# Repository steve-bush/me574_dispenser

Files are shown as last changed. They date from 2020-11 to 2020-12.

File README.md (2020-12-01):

# Plague Destroyer 3000

Below are the steps for setting up group 6's hand sanitizer dispenser for either home use or company use. The files for setting up the logoff scripts are located in the `logoff_scripts` directory. The part files for 3D printing are located in the `printing` directory. Lastly, the Arduino code is located in the `dispenser` directory.

## Printing

Use whatever printing software you prefer for slicing the STL files. We used Cura for our own set up to get usable G code. We used PLA+ at 225 C ejection temperature, 75 C bed temperature, 55% infill, a wall count of 3, and a 45 mm/s print speed.

## Assembly

1. Watch instruction [video](https://youtu.be/RnLYFoYw21w) for more information on the following steps.
2. Assemble PCB board according to the [schematic](https://github.com/steve-bush/me574_dispenser/blob/master/pcb/PCB_Schematic.PNG) and [BOM](https://github.com/steve-bush/me574_dispenser/blob/master/pcb/BOM_PCB%20Design_2020-11-05_15-47-10.csv) provided.
3. Drill 3/8in hole into top corner of sanitizer bottle.
4. Assemble Base Lid to Top using provided dowel pins.
5. Route USB cable through base inserting mini USB through bottom of base leaving 3 in of cable through top of base. Make sure USB cable is secured into notch on bottom of base.
6. Attach Pump to Pump Holder, making sure the suction port of the pump is at the base of the Pump Mount.
7. Install tubing into pump outlet, use twisting motion for proper installation.
8. Insert Pump and Pump mount into sanitizer bottle. Making sure that pump mount is sitting flush with the sanitizer bottle and pump outlet is facing towards hole in bottle.
9. Route wiring from pump and tubing through grommet hole in sanitizer bottle from the inside of the bottle to the outside.
10. Slide grommet over electrical cable beyond heat shrink tubing, then squeeze and insert tubing through grommet.
11. Insert grommet securely into hole of bottle.
12. Install grommet into sanitizer bottle.
13. Install sanitizer bottle into base with tubing towards right side of base when viewing from bottle side.
14. Insert LED holder into Top.
15. Mount assembled Base Lid and Top to the base using 2 of the provided screws, making sure USB cable and tubing is routed through slot in base and to not overtighten screws.
16. Flip assembly onto top.
17. Route tubing to far side of Top ensuring enough tube is allowed to reach nozzle.
18. Plug USB cord into Arduino Nano on PCB Board.
19. Insert PCB board into Top above tubing and secure with 2 of the provided screws making sure that the red/green Led is secured into LED holder and tubing and wiring is not pinched.
20. Install top cover making sure tubing is aligned with nozzle.
21. Plug in motor to motor wire from PCB board with correct polarity.
22. Install sanitizer bottle lid onto bottle.
23. Install mid cover onto front of sanitizer.
24. Plug in USB to 5V 1A power source or Computer USB port.

## Software

There are 2 different scripts than can be chosen from to enable the device to block login. The first script is `dispenser_ping_secure.ps1` which is the recommended script to use. It will block login whether the dispenser is plugged in or not. The other script named, `dispenser_ping.ps1`, will stop working when the device is unpluggled which may be desired for people without much computer knowledge.

When setting up the script to be run on login, the company's administrative software should be used and set up to run for non-admin or non-IT users. I give steps below to setting it up with Windows Group Policy and also with Task Scheduler. These would be available to anyone and the steps should be similar for whatever other administrative software used.

To setup using Group Policy:
1. Download files from GitHub.
2. Open mmc from the Windows search bar
3. Select File > Add/Remove Snap-in..
4. Select the Group Policy Object from the snap-in list
5. Click Add >
6. Select Browse.. then Users on the top options
7. Select Non-Administrators then OK
8. Click OK and double-click on the policy object
9. Select User Configuration > Windows Settings > Scripts (Logon/Logoff) > Logon
10. Select add and move the .ps1 file into the default browsing location (it will be hidden)
11. Now go back to the add screen and select the .ps1 file
12. Close and save the mmc screen

To setup with Task Scheduler:
1. Open Task Scheduler from the Windows search bar
2. Select Create Task...
3. Set the name to whatever you like, the group that is desired, and configuration to Windows 10.
4. Under the Triggers tab, select New and then set task to run on login
5. Under the Actions tab, select New and set the task to run either Powershell script
6. Close and save the new task.

Lastly, the Arduino [code](https://github.com/steve-bush/me574_dispenser/tree/master/dispenser) will need to be uploaded to either an Arduino Nano or Mega.

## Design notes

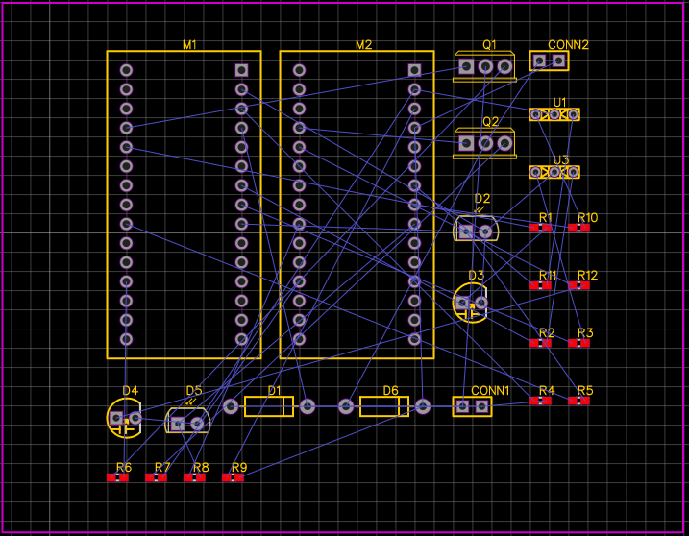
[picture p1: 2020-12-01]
pcb/PCB_Schematic.PNG

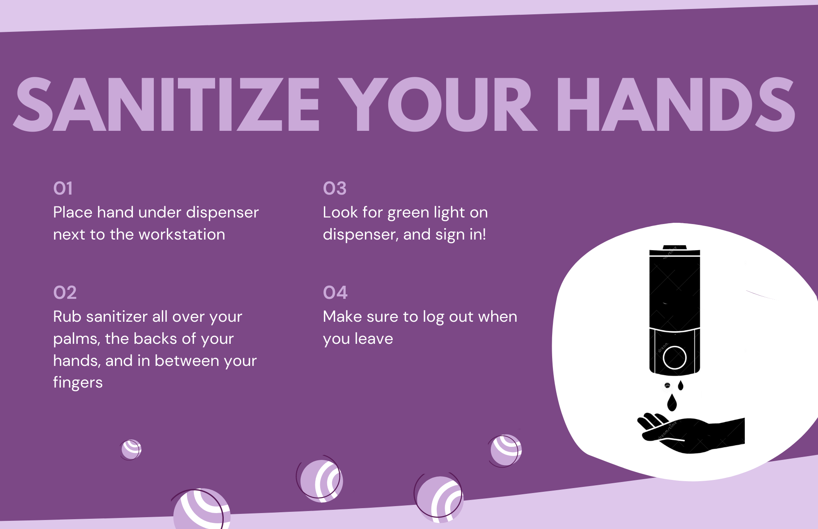
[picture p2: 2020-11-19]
Blue_and_White_Handwashing_101_Landscape_COVID_Flyer.png

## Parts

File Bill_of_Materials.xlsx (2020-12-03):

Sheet: Bill of Materials
Bill of Materials
Item # | Item | Part Number | Source | Cost | Qty. | Ext. Cost | Item # | Link
1 | 3x5mm Silicon Rubber Tubing | 372114317823 | Ebay, giorgio11185 | $14.36 | 0.01333333333 | $0.19 | 1 | https://www.ebay.com/itm/US-Stock-50ft-OD-5mm-ID-3mm-Silicone-Food-Grade-Rubber-Tube-Hose-Pipe/372114317823
2 | Jar w/Cap | 137579 | US Plastic Corp | $0.87 | 1 | $0.87 | 2 | https://www.usplastic.com/catalog/item.aspx?itemid=137579
3 | Submersible Pump | 292F517 | Alibaba, Fbele | $0.33 | 1 | $0.33 | 3 | https://www.alibaba.com/product-detail/DC-3V-mini-water-pump-Horizontal_1600055883828.html
4 | PCB |  | PCBWay | $0.62 | 1 | $0.62 | 4
5 | 3ft USB type A to type B mini | 3021055-03 | Mouser | $0.98 | 1 | $0.98 | 5 | https://www.mouser.com/ProductDetail/Qualtek/3021055-03?qs=MLItCLRbWswd6xwF2kMv5g%3D%3D
6 | Rubber Grommet 1/4" ID, 3/8" slot diamter | 9600K25 | McMastercarr | $0.07 | 1 | $0.07 | 6 | https://www.mcmaster.com/9600K25/
7 | #4 x 3/4" Thread Forming Screws for Plastics (48-2) / Phillips / Pan Head / Steel / Zinc | 231428 | Fastener Super Store | $0.01 | 4 | $0.06 | 7 | https://www.fastenersuperstore.com/products/231428/thread-forming-screws
8 | Base - injection molded |  | Xometry | $1.20 | 1 | $1.20 | 8
9 | Base Lid - IM |  | Xometry | $1.02 | 1 | $1.02 | 9
10 | Mid Level Cover - IM |  | Xometry | $0.75 | 1 | $0.75 | 10
11 | Top - IM |  | Xometry | $1.42 | 1 | $1.42 | 11
12 | Top Cover - IM |  | Xometry | $1.04 | 1 | $1.04 | 12
13 | Pump holder - IM |  | Xometry | $0.40 | 1 | $0.40 | 13
14 | Tooling cost per unit |  | Xometry | $1.12 | 1 | $1.12 | 14
15 | Labor Cost (USA) |  | USA Labor (PayScale) | $13.45 | 0.088736 | $1.19 | 15 | https://www.payscale.com/research/US/Job=Assembly_Line_Worker/Hourly_Rate
 |  |  |  |  | Total | $11.26
 | Tooling cost |  |  | $31221.00

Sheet: 2nd and 3rd Quotes
2nd and 3rd Quotes
Item # | Item | Part Number | Source | Cost | Qty. | Ext. Cost | Item # | Link
1 | 3mm x 5mm Silicon tubing | 3184K288 | McMaster-Carr | $0.67 | 1 | $0.67 | 1
1 | 3mm x 5mm Silicon tubing | SKU: ST-35 | MODDIY | $0.99 | 0.6666666667 | $0.66 | 1 | https://www.moddiy.com/products/High-Quality-Food-Grade-Flexible-Silicone-Tubing-3mm-ID-x-5mm-OD.html
1 | 3x5mm Silicon Rubber Tubing |  | Ebay, giorgio11185 | $14.36 | 0.01333333333 | $0.19 | 1 | https://www.ebay.com/itm/US-Stock-50ft-OD-5mm-ID-3mm-Silicone-Food-Grade-Rubber-Tube-Hose-Pipe/372114317823
2 | 32oz Clear PET container with grips without cap | 3471B03-B | Berlin Packaging | $0.96 | 1 | $0.96 | 2 | https://www.berlinpackaging.com/3471b03-b-32-oz-clear-petg-plastic-gripper-containers-cap-not-included/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
2 | Clear PET 32oz Jar/cap | CP-B124 | Premium Vials | $159.99 | 0.007936507937 | $1.27 | 2 | https://www.premiumvials.com/pk-of-126-32-oz-clear-pet-square-grip-container-with-89-400-neck-finish/
2 | Jar w/Cap |  | US Plastic Corp | $0.87 | 1 | $0.87 | 2 | https://www.usplastic.com/catalog/item.aspx?itemid=137579
3 | Submersible pump, 3-5v | B08D986N3V | Amazon - Sen Mod | $12.99 | 10 | $1.30 | 3 | https://www.amazon.com/Senmod-Silent-Submersible-Computer-Cooled/dp/B08D986N3V?hvadid=475811883826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
3 | Submersible pump 3-6v | #00002 | Ebay - Light in the Box | $4.19 | 1 | $4.19 | 3 | https://www.google.com/shopping/product/1?q=5v+aquarium+pump
3 | Submersible Pump, 5v |  | Alibaba, Fbele | $0.33 | 1 | $0.33 | 3 | https://www.alibaba.com/product-detail/DC-3V-mini-water-pump-Horizontal_1600055883828.html
4 | PCB |  | Rush PCB | $10.85 | 1 | $10.85 | 4
4 | PCB |  | PCBWay | $0.62 | 1 | $0.62 | 4
4 | PCB |  | 4PCB | $3.32 | 1 | $3.32 | 4
5 | 1ft USB2.0 A Male to Mini-B 5-pin Male Cable | U2105-1101 | Cable Leader | $0.77 | 1 | $0.77 | 5 | https://www.cableleader.com/1ft-usb2-0-a-male-to-mini-b-5-pin-male-cable.html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
5 | USB 2.0 Cable, A-Male/Mini B-Male, 5-Pin, Hi-Speed 480Mbps, 3FT | USB2-3017-ABM5 | Primus Cable | $1.13 | 1 | $1.13 | 5 | https://www.primuscable.com/products/usb-2-0-cable-a-malemini-b-male-5-pin-hi-speed-480mbps-1ft-3ft-6ft-10ft-15ft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
5 | 3ft USB type A to type B mini | 3021055-03 | Mouser | $0.98 | 1 | $0.98 | 5 | https://www.mouser.com/ProductDetail/Qualtek/3021055-03?qs=MLItCLRbWswd6xwF2kMv5g%3D%3D
6 | Rounded Head Thread-Forming Screws | 97349A418 | McMaster-Carr | $0.06 | 4 | $0.25 | 6 | https://www.mcmaster.com/97349A417/
6 | #4-20 x 3/4 in Zinc-Plated Case Hardened Steel Thread Forming Screw with Pan Head Type, 100 PK | 5JE99 | Grianger Industrial | $0.16 | 4 | $0.65 | 6 | https://www.grainger.com/product/TAMPER-PRUF-SCREW-4-20-x-3-4-in-Zinc-Plated-5JE99
6 | #4 x 3/4" Thread Forming Screws for Plastics (48-2) / Phillips / Pan Head / Steel / Zinc | 231428 | Fastener Super Store | $0.01 | 4 | $0.06 | 6 | https://www.fastenersuperstore.com/products/231428/thread-forming-screws
8 | Base - injection molded |  | Xometry | $1.20 | 1 | $1.20 | 8
8 | Base - injection molded |  | Texas Injection | $1.93 | 1 |  | 8
8 | Base - injection molded |  | Protolabs | $6.38 | 1 | $6.38 | 8
9 | Base Lid - IM |  | Xometry | $1.02 | 1 | $1.02 | 9
9 | Base Lid - IM |  | Texas Injection | $0.82 | 1 | $0.82 | 9
9 | Base Lid - IM |  | Protolabs | $3.81 | 1 | $3.81 | 9
10 | Mid Level Cover - IM |  | Xometry | $0.75 | 1 | $0.75 | 10
10 | Mid Level Cover - IM |  | Texas Injection | $1.04 | 1 | $1.04 | 10
10 | Mid Level Cover - IM |  | Protolabs | $4.70 | 1 | $4.70 | 10
11 | Top - IM |  | Xometry | $1.42 | 1 | $1.42 | 11
11 | Top - IM |  | Texas Injection | $0.99 | 1 | $0.99 | 11
11 | Top - IM |  | Protolabs | $4.61 | 1 | $4.61 | 11
12 | Top Cover - IM |  | Xometry | $1.04 | 1 | $1.04 | 12
13 | Pump holder |  | 3D Printed | $0.42 | 1 | $0.42 | 13
14 | Tooling cost per unit |  | Xometry | $1.00 | 1 | $1.00 | 14
14 | Tooling cost per unit |  | Texas Injection | $1.55 | 1 | $1.55 | 14
14 | Tooling cost per unit |  | Protolabs | $0.99 | 1 | $0.99 | 14
15 | Labor Cost (USA) |  | USA Labor (PayScale) | $13.45 | 0.088736 | $1.19 | 15 | https://www.payscale.com/research/US/Job=Assembly_Line_Worker/Hourly_Rate

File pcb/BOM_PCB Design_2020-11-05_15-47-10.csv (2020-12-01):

ID | Name | Designator | Footprint | Quantity | Manufacturer Part | Manufacturer | Supplier | Supplier Part
1 | IRF510 | Q1,Q2 | TO220 | 2 | IRF510PBF | IR | LCSC | C2596
2 | MICROCONTROLLER | M1,M2 | ARDUINO NANO | 2 | PIC18F2321-I/SO | Microchip Tech | LCSC | C184141
3 | IR LED | D3,D4 | LED2-2.54-D5.0MM | 2 | 2A5Y3UD09 LED | KENTO | LCSC | C3651
4 | 2 pin header | CONN1,CONN2 | 2 PIN HEADER | 2 | Female header1*2P | BOOMELE | LCSC | C66509
5 | 120 OHM | R4,R9 | 0603-RES | 2 | 1206W4J0124T5E | UniOhm | LCSC | C25648
6 | PHOTODIODE | D2,D5 | PHOTODIODE_SFH225 | 2 | DK5V45R10 | DK | LCSC | C94730
7 | DIODE IN4001 | D1,D6 | DIODE-1N4001 | 2 | DK5V45R10 | DK | LCSC | C94730
8 | RG LED | U3,U1 | LED-DUALCOLOR-3MM | 2 | 3528 Red LED | KENTO | LCSC | C2305
9 | 300OHM-1_10W-1%(0603) | R1,R12 | 0603-RES | 2 | RD 3WS 300R J T/B A1 | TyoHM | LCSC | C433811
10 | 300 OHM | R2,R3,R10,R11 | 0603-RES | 4 | SMF 3W 300R J | TyoHM | LCSC | C395116
11 | 10k OHM | R5,R6,R7,R8 | 0603-RES | 4 | MF58 103F3435 | Nanjing Shiheng Elec | LCSC | C123387

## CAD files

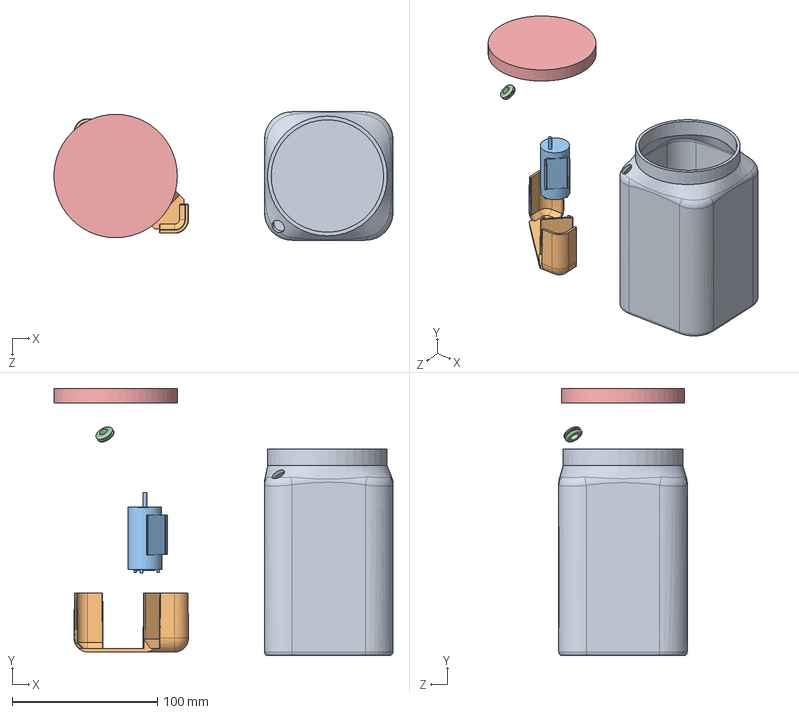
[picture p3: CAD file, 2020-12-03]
solidworks/Bottle Assembly.SLDASM
233.7 x 184.3 x 88.6 mm
Bottle
Pump holder
Liquid Pump
Rubber Grommet
BottleLid

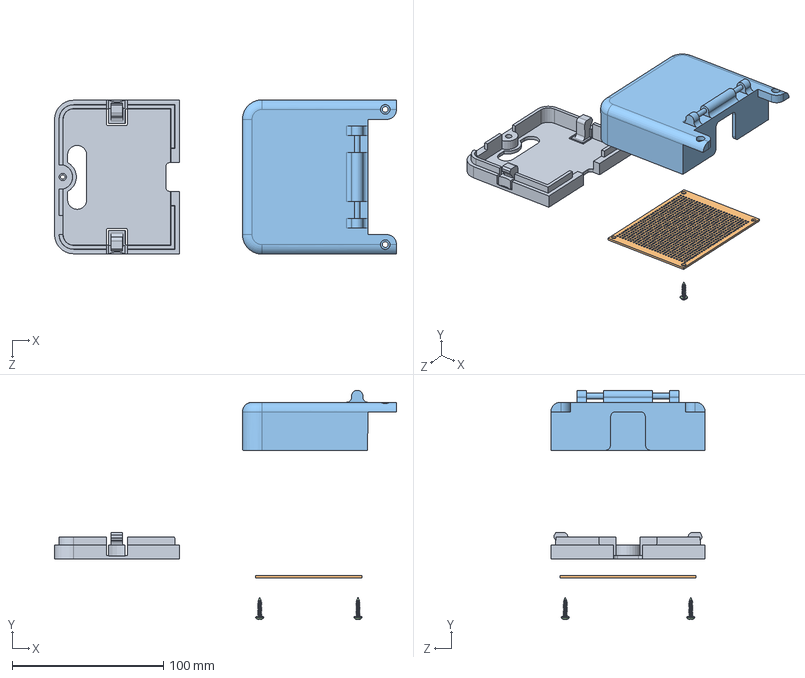
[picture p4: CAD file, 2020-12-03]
solidworks/Top Assembly.SLDASM
226.1 x 151.6 x 102.0 mm
Top Under Cover
Circuit Board
Top
92470A110_PAN HEAD PHILLIPS SCREW FOR SHEET METAL x 2

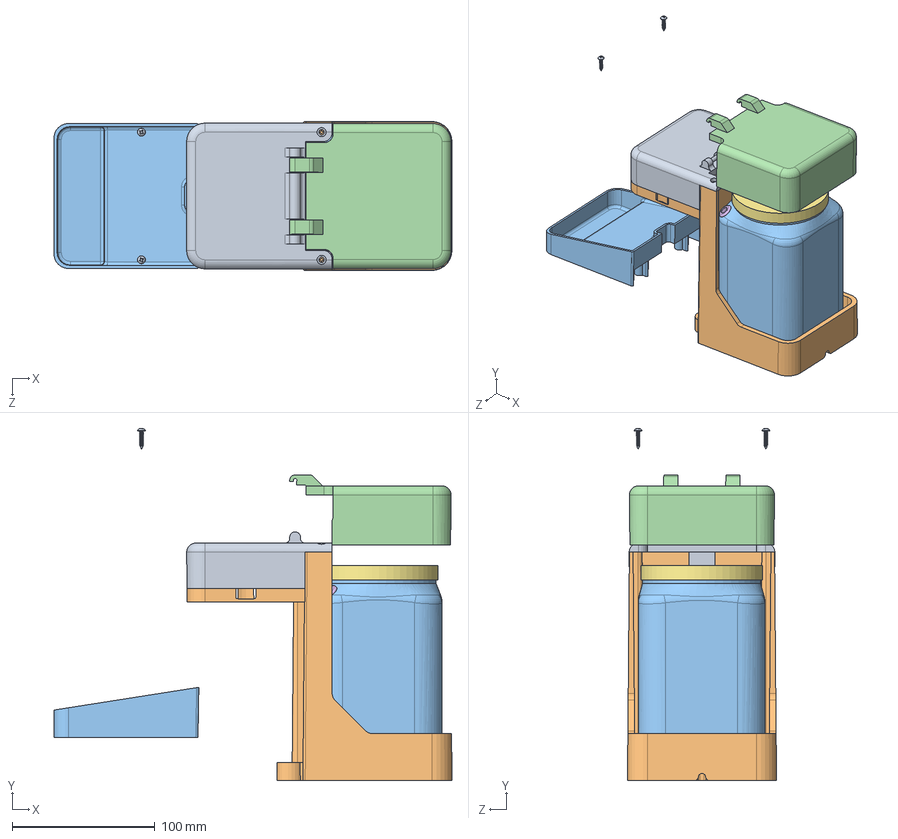
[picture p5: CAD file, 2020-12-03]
solidworks/Full Assembly.SLDASM
278.6 x 246.7 x 104.4 mm
Bottle
Pump holder
Liquid Pump
Rubber Grommet
BottleLid
Top Under Cover
Circuit Board
Top
92470A110_PAN HEAD PHILLIPS SCREW FOR SHEET METAL x 4
Base
Drip Tray
BaseLid

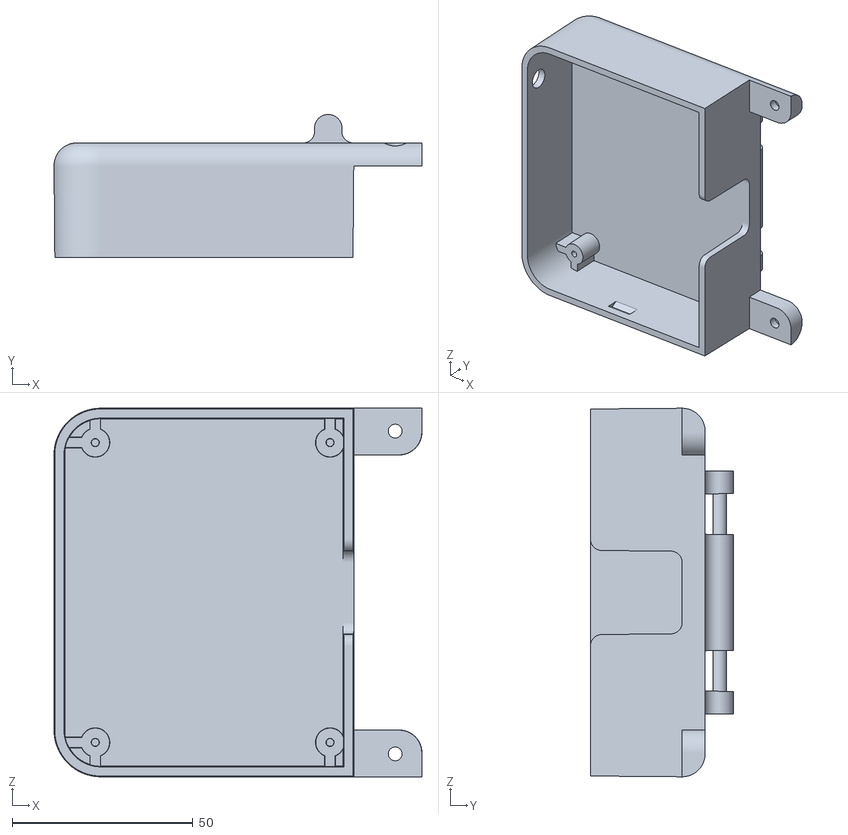
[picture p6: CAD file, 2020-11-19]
printing/Top 11_5.STL
101.9 x 39.6 x 102.0

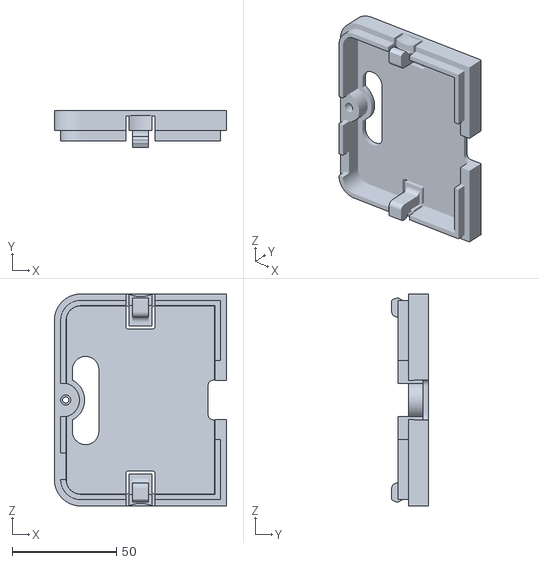
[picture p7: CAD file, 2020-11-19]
printing/Top cover10_15.STL
82.6 x 17.6 x 101.6

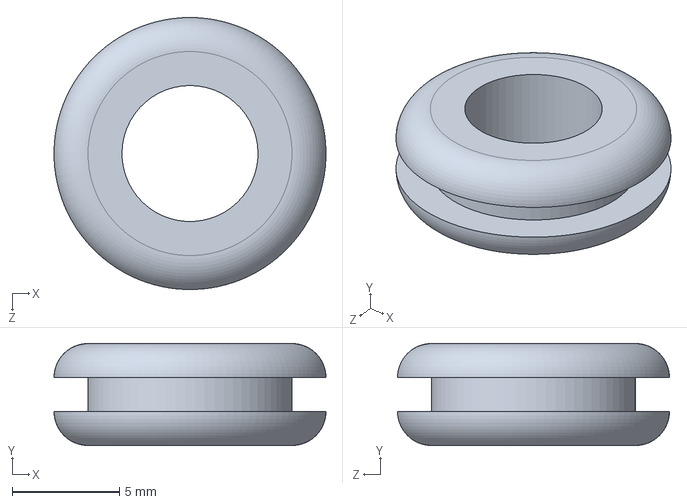
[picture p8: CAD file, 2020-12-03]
solidworks/Rubber Grommet.SLDPRT
12.7 x 4.76 x 12.7 mm

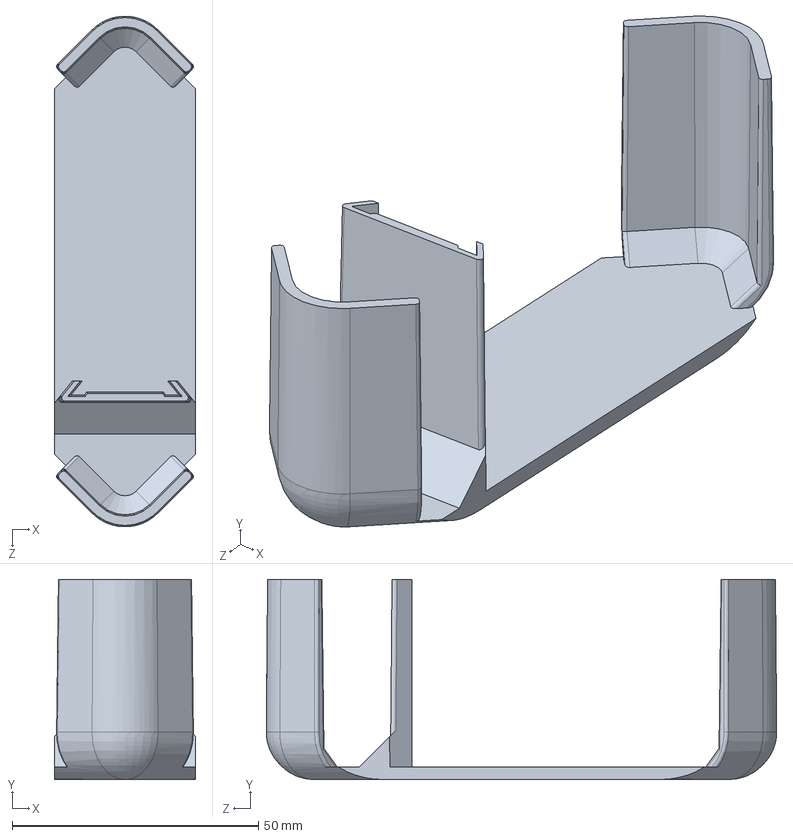
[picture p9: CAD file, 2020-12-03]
solidworks/Pump holder.SLDPRT
28.7 x 40.6 x 103.7 mm

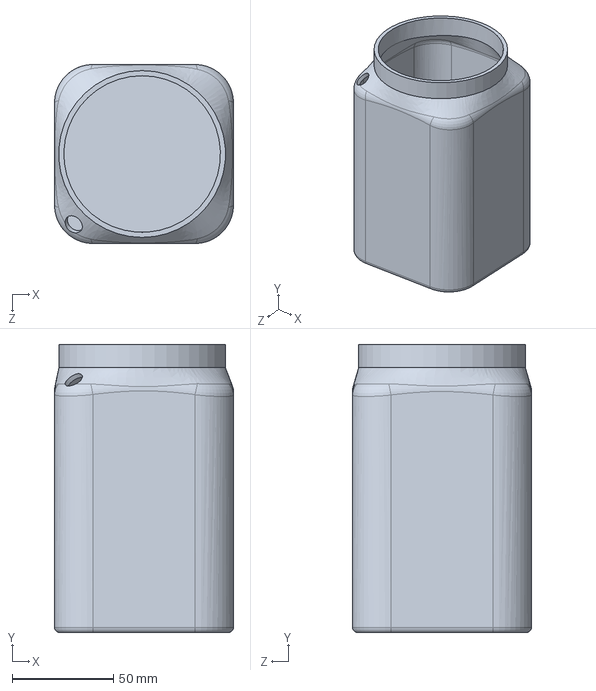
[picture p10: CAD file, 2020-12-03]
solidworks/Bottle.SLDPRT
88.6 x 142.5 x 88.6 mm

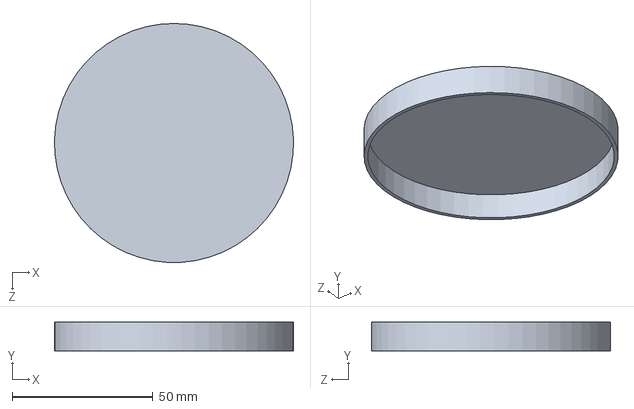
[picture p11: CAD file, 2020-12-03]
solidworks/BottleLid.SLDPRT
85.1 x 10.2 x 85.1 mm

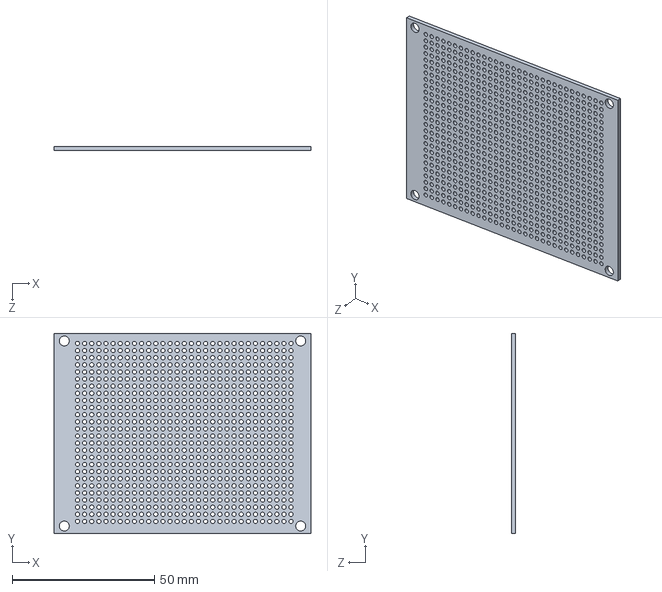
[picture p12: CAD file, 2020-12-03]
solidworks/Circuit Board.SLDPRT
90.2 x 70.2 x 1.50 mm

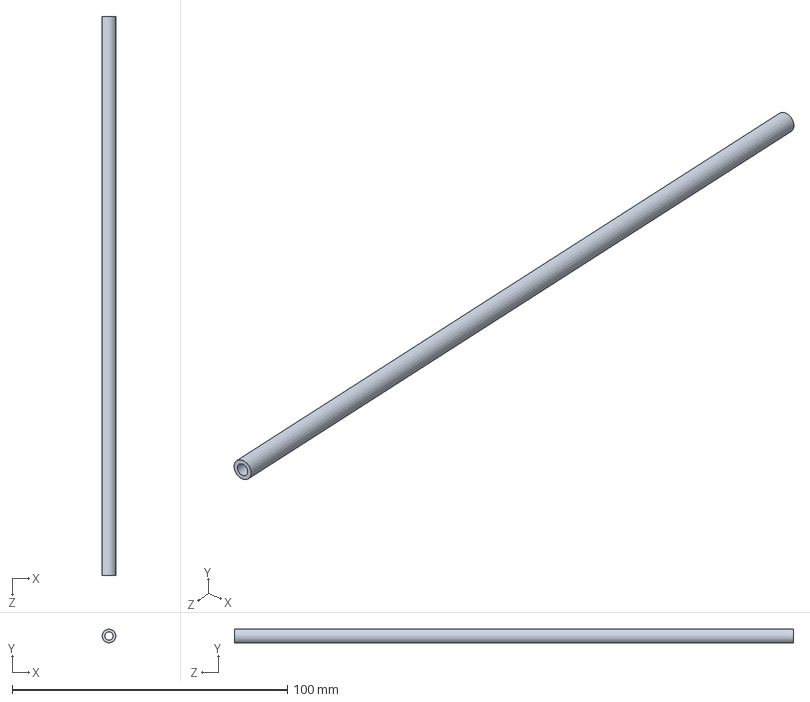
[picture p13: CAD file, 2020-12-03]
solidworks/Transfer Tube.SLDPRT
5.00 x 5.00 x 203.2 mm

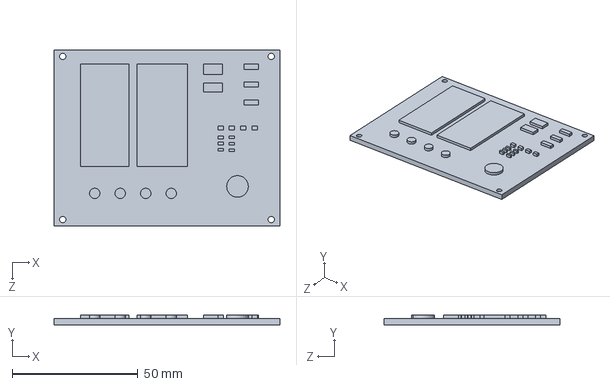
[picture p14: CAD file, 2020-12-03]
solidworks/PCB.SLDPRT
90.0 x 3.81 x 70.0 mm

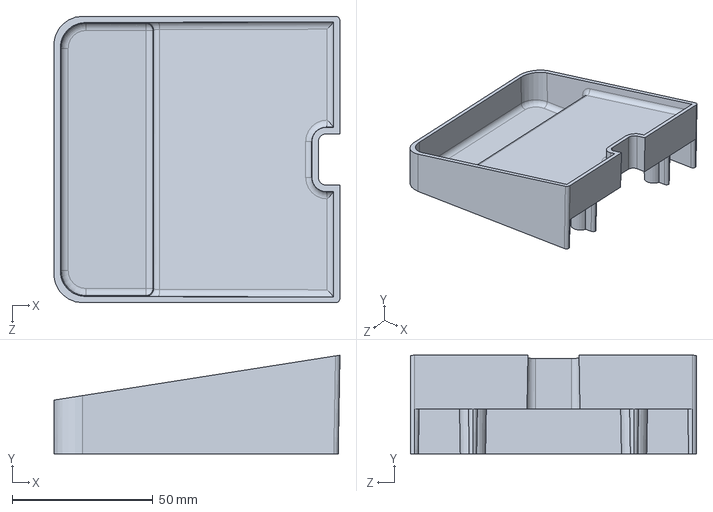
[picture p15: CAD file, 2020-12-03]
solidworks/Drip Tray.SLDPRT
101.4 x 35.0 x 101.6 mm

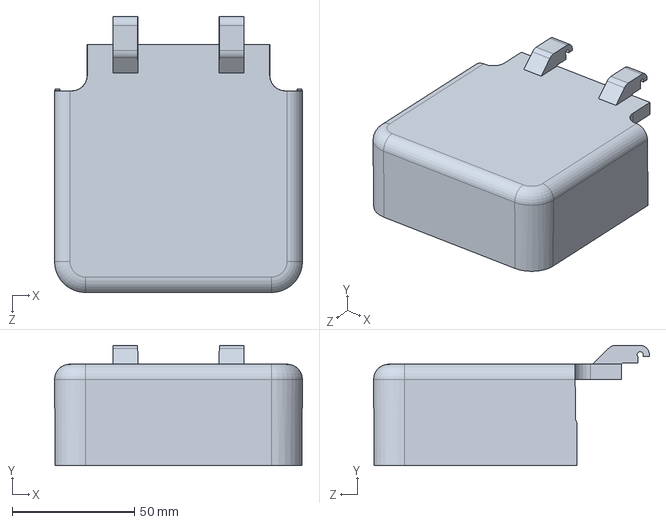
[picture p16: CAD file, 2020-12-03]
solidworks/BaseLid.SLDPRT
101.5 x 49.1 x 113.0 mm

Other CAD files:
solidworks/Top.SLDPRT
solidworks/Top Under Cover.SLDPRT
solidworks/Base.SLDPRT
solidworks/Liquid Pump.SLDPRT
printing/Base.STL
solidworks/92470A110_PAN HEAD PHILLIPS SCREW FOR SHEET METAL.SLDPRT

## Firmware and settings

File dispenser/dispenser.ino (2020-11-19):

#include "dispenser.h"

enum DispenserState { Unwashed, Dispense, Washed } dispenserState;
unsigned long SensorTime; // Timer for when sensor detects hand.
unsigned long WashTime; // Timer for end of washed state
unsigned long DispenseTime; // Timer for length of dispense state
bool wash_flag; // Flag for deciding what to send
unsigned int previous_readings[NUM_READINGS];
unsigned int new_readings[NUM_READINGS];
int index = 0;
// 1 minute 30 seconds to log on (milliseconds)
const unsigned long WASH_TIMEOUT = 90000;

void set_to_washed() {
  wash_flag = WASHED; // Indicate that button is pressed
  analogWrite(RED_LED, 0); // Turn off red first so both LEDs are not on
  analogWrite(GREEN_LED, 255); // Turn on green to indicate login time
  WashTime = millis(); // Begine wash_timer for timeout
}

void set_to_unwashed() {
  wash_flag = UNWASHED; // Indicate unwashed
  analogWrite(GREEN_LED, 0); // Turn off green first so both LEDs are not on
  analogWrite(RED_LED, 255); // Turn on red to indicate washing hands
}

void initialize_sensor() {
  // Set up the sensor reading arrayss
  for (int i = 0; i < NUM_READINGS; i++) {
    previous_readings[i] = analogRead(PHOTODIODE_SENSOR);
    new_readings[i] = analogRead(PHOTODIODE_SENSOR);
  }
}

bool read_sensor() {
  if (millis() - SensorTime < SENSOR_DELAY){
    return false;
  }
  //Add sensor reading into the array
  previous_readings[index] = new_readings[index];
  new_readings[index] = analogRead(PHOTODIODE_SENSOR);

  // Move index down the array
  index++;

  // Loop index back to 0 if past array bounds
  if (index > NUM_READINGS - 1) {
    index = 0;
  }

  // Initialize average readings variables
  float previous_ave = 0;
  float new_ave = 0;
  // Add up the previous and new readings arrays
  for (int i = 0; i < NUM_READINGS; i++) {
    previous_ave += previous_readings[i];
    new_ave += new_readings[i];
  }

  // Calculate the average of the readings
  previous_ave /= NUM_READINGS;
  new_ave /= NUM_READINGS;

  // Update SensorTime for delay
  SensorTime = millis();
  
  if (previous_ave - new_ave > THRESHOLD_CHANGE) {
    return true;
  }
  else {
    return false;
  }
}

void setup() {
  // Setup pins
  pinMode(GREEN_LED, OUTPUT);
  pinMode(RED_LED, OUTPUT);
  pinMode(MOTOR, OUTPUT);
  Serial.begin(9600); // Set baud rate to 9600.
  pinMode(PHOTODIODE_SENSOR, INPUT);
  pinMode(PHOTODIODE_POWER, OUTPUT);
  digitalWrite(PHOTODIODE_POWER, HIGH);
  pinMode(IR_LED, OUTPUT);
  digitalWrite(IR_LED, HIGH);
  set_to_unwashed();
  initialize_sensor();
  dispenserState = Unwashed; // Set state back to unwashed
} // setup()

void loop() {
  // Check for ping from pc
  if (Serial.available() > 0) {
    Serial.readString(); // Read in passed
    // Send state of wash_flag to pc
    if (wash_flag) {
      Serial.println("Washed"); // Indicate that hands have been washed
      set_to_unwashed();
      dispenserState = Unwashed; // Set state back to unwashed
    }
    else {
      Serial.println("Unwashed"); // Indicate that hands are not washed
    }
  }

  switch (dispenserState) {
    case Unwashed:
      if (read_sensor()) { // If hand detected.
        DispenseTime = millis(); // Record time of hand detection.
        analogWrite(MOTOR, 255);
        set_to_washed();
        dispenserState = Dispense; // Set state back to unwashed
      }
      break;

    case Dispense:
      read_sensor();
      if (millis() - DispenseTime >= DISPENCE_TIME) {
        analogWrite(MOTOR, 0);
        set_to_washed();
        dispenserState = Washed; // Set state to washed
      }
      break;

    case Washed:
      if (read_sensor() && millis() - DispenseTime >= DISPENCE_DELAY) { // If hand detected.
        analogWrite(MOTOR, 255);
        DispenseTime = millis(); // Record time of hand detection.
        dispenserState = Dispense; // Move to intial detection state.
      }
      else if (millis() - WashTime >= WASH_TIMEOUT) {
        set_to_unwashed();
        dispenserState = Unwashed; // Set state back to unwashed
      }
      break;
  }
} // loop()

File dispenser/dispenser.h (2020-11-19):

// Bools to be used for the wash_flag
#define WASHED true
#define UNWASHED false
// Pin assignments
#define RED_LED A5
#define GREEN_LED A4
#define MOTOR  9 // D9
#define PHOTODIODE_SENSOR A3
#define PHOTODIODE_POWER 2 //D2
#define IR_LED 6 // D6
// Threshold for defining hand detection.
#define THRESHOLD_CHANGE 30
#define NUM_READINGS 2
#define SENSOR_DELAY 100
// Amount of time to dispense.
#define DISPENCE_TIME 875 // .875 second
#define DISPENCE_DELAY 3000 // 3 seconds

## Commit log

2020-09-14 Added full prototype code, renamed powershell script, and rearanged folders
2020-11-19 Added more steps
    [Base.STL, Top 11_5.STL, Top cover10_15.STL]
2020-11-26 Formatting. Needs circuit
2020-11-26 Editting. Still needs circuitry
2020-12-01 Added circuit info
    [BOM_PCB Design_2020-11-05_15-47-10.csv]
2020-12-01 Circuit links
2020-12-03 BOM and Solidworks files
    [92470A110_PAN HEAD PHILLIPS SCREW FOR SHEET METAL.SLDPRT, Base.SLDPRT, BaseLid.SLDPRT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]
